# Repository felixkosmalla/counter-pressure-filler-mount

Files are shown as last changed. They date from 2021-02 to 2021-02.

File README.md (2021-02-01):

# Counter Pressure Filler Mount
Source Files and Documentation for a Mount for the Cheap Counter Pressure Fillers

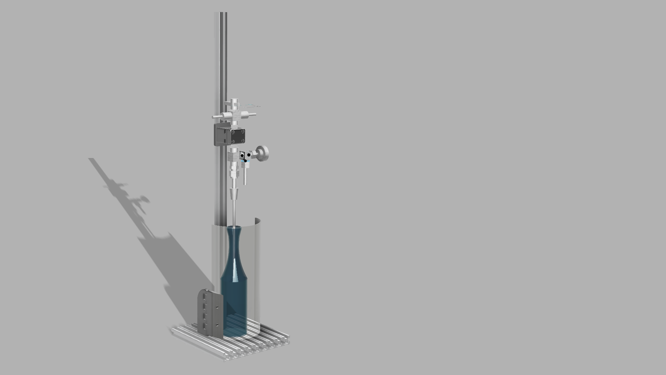
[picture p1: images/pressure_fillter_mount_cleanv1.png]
Counter Pressure Filler Mount


# Disclaimer
I assume a certain degree of self awareness, responsibility and common sense of the reader. Use these files and resources at your own risk. I am not responsible for any damage to humans and or things that may arise when using a counter pressure filler with this rig. I also do not guarantee any degree of completeness for the provided documents and files.

# Tools and Resources needed
* 3D Printer (or someone you know that has a 3D Printer), I used PETG and a Prusa MK3s, 20% infill, with supports
* Laser Cutter (optional)
* Small screwdriver to clean up 3D print
* Allen Keys
* Hot Glue Gun (or wood glue?)
* Heat Gun to form the shield
* Hammer
* 5.5mm drill bit & drill

# Bill of Material
Links for convenience, no affiliation. OpenBuilds 2020 V-Slot Profiles are used as structural base.

| Product | Link | Amount |
| --- | --- | --- |
| Counter Pressure Filler | https://www.amazon.de/gp/product/B07TQT33DP | 1 |
| Openbuilds Gantry Plate | https://www.amazon.de/dp/B07SLZFWKF | 1 |
| Angle for 2020 Openbuilds Profiles + Nuts + Bolts | gone.., maybe print it https://www.thingiverse.com/thing:105900 | 1 |
| Nuts for 2020 Openbuilds Profile | gone.., also maybe print it https://www.thingiverse.com/thing:3050607 | 2 |
| M5x10 | Hardware Store | 4 |
| M5 Nut | Hardware Store | 6 |
| M5 Nut | Hardware Store | 6 |
| 2020 OpenBuilds Profile, 20cm | https://shop.myhobby-cnc.de/bauteile/mechanische-bauteile/profile/66/openbuilds-profil-20x20mm | 9 |
| 2020 OpenBuilds Profile, 70cm | https://shop.myhobby-cnc.de/bauteile/mechanische-bauteile/profile/66/openbuilds-profil-20x20mm | 1 |
| 2mm Plexiglas, 25cm x 18.5cm | Hardware Store? | 1 |
| 3mm A3 MDF sheet or plywood | Hardware Store? | 1, maybe 2 to be sure |

# Parts to Print

## 1x Shield Mount
This part can be printed as a whole, standing up. A little carfull bending will losen the hinge. Clean it with something pointy like a flat head screwdriver.

## 1x Bottom and Top Clamp
The notches in the top clamp part need to be printed with support structures and then cleaned with a screwdriver or something [hook-y](https://www.amazon.de/dp/B07JP662XM). This is tedious, but it did fit for me in the end.
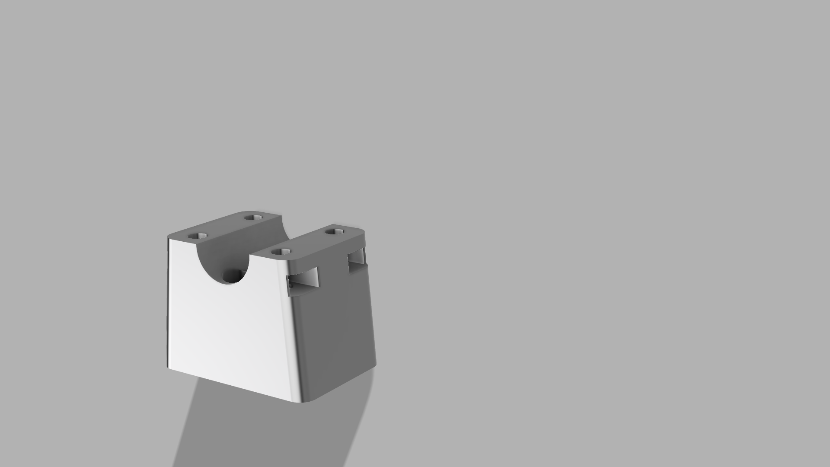
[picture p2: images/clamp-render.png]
Clamp Bottom that needs to be cleaned


## 16x OpenBuilds Connector
https://www.thingiverse.com/thing:2160166
Maybe you need to scale this, see instructions!

# Assemble

## Base
Use the OpenBuild Connectors and a little persuasian with a hammer to connect the profiles to form a base.

## Stem
Mount the stem with the angle at the 5th shorter profile.

## Shield Mount
Mount the shield mount with two nuts and bolts at the 7th profile.

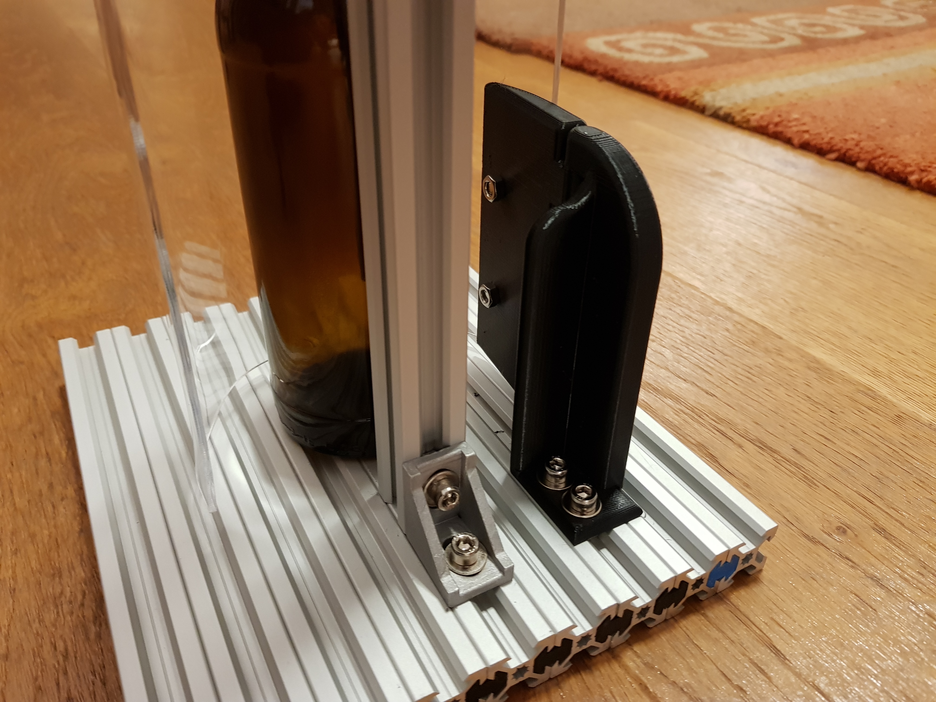
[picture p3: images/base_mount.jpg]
Assmebled base and mounted stem and shield mount


## Shield
Drill the holes according to the drawing or use a laser cuttter and the provided DXF file.
Cut 4 Rings and 6 Ribs out of the MDF according to the pattern in the PDF directory. 
Glue the bending rig together with hotglue or whatever you have at hand.
Without removing the protective layer from the plexiglass sheet, wedge the sheet in the bending rig.
**Make sure that the long end is pointing upwards.**
Start heating up the sheet and smooth, horizontal movements until the sheet starts bending. Work your way up until the sheet is completely bend around the rig.

After cooling, mount the Shield on the shield mount using the M5X10 screws.

## Clamp
Squeece 4 Nuts in the recesses of the clamp base. Mount the base on the gantry plate.
Clamp the pressure filler between the clamp base and top using 4 screws, tightening them carefulle and diagonally.
Slide the gantry on the stem.

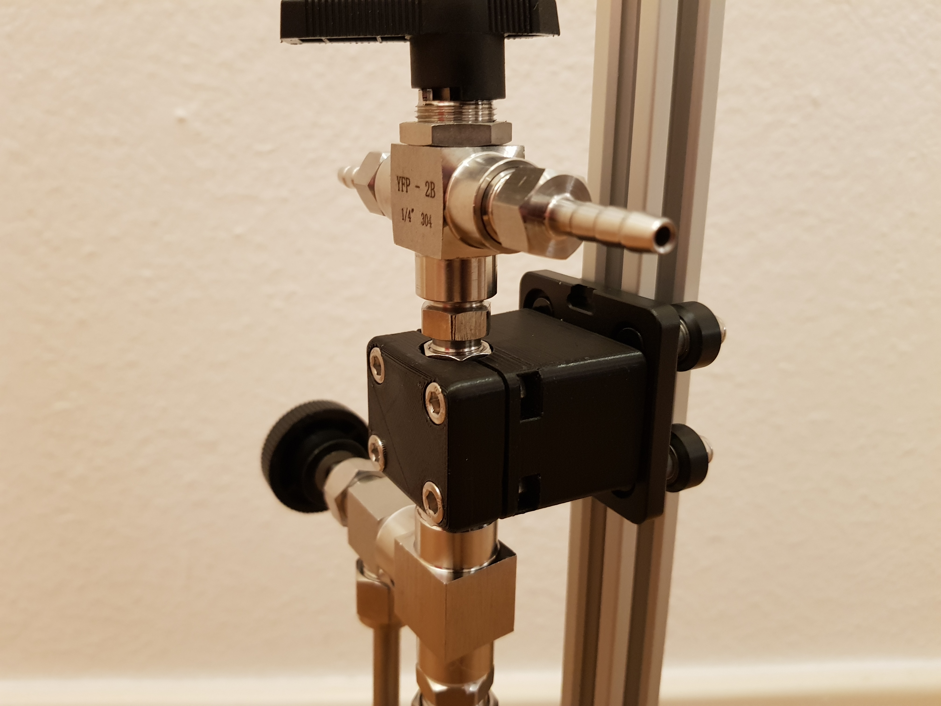
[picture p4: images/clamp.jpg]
Clamped pressure filler


# Happy Botteling!
Any comments or improvements? Either submit an issue or create a pull request. If you found this useful, consider [buying me a beer](https://paypal.me/felixkosmalla) ;) 

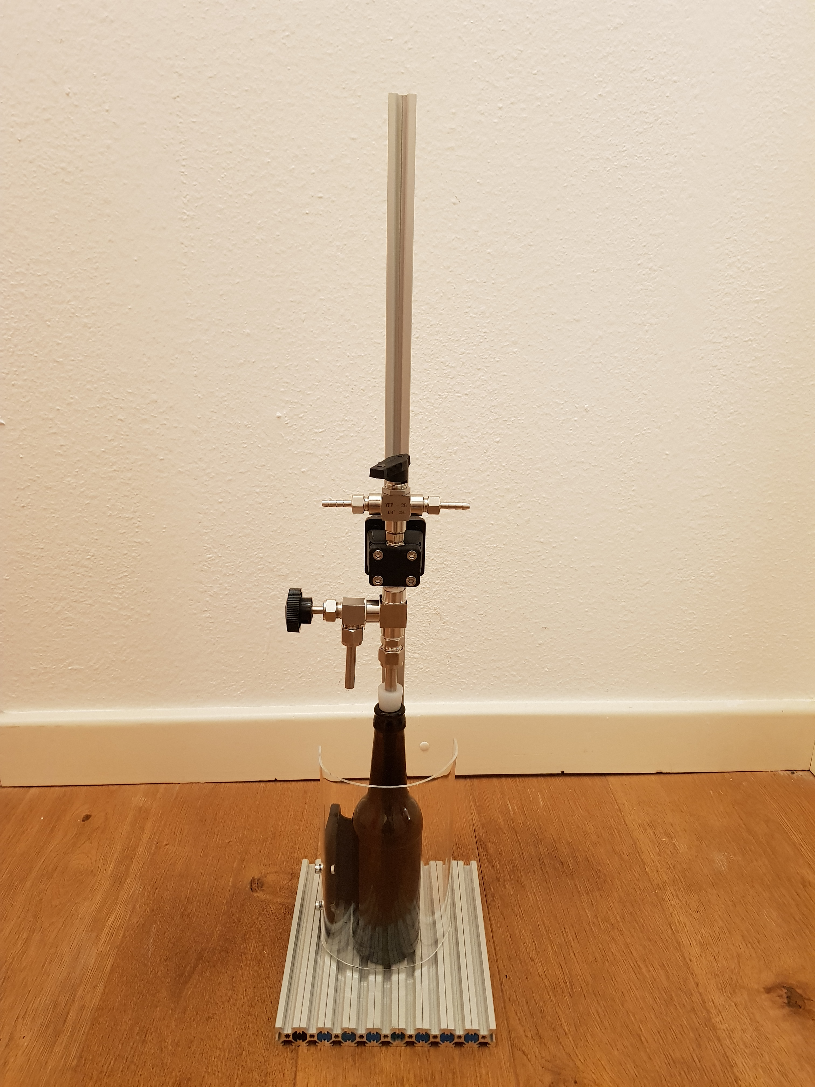
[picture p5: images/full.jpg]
pressure filler mount pressure filler mount

As you can see, I did **not** align the long side upward on the bending rig, resultin in a shorter shield towards the top that I had to cut towards the back. Don't be like me, be smart!

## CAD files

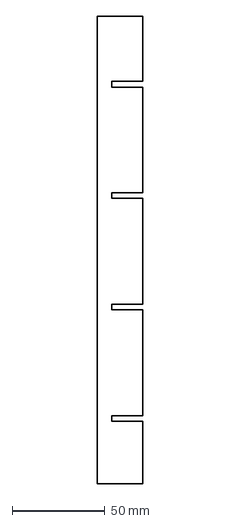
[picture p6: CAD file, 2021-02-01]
DXF/bending_frame_rib.dxf
24.8 x 251.5 mm

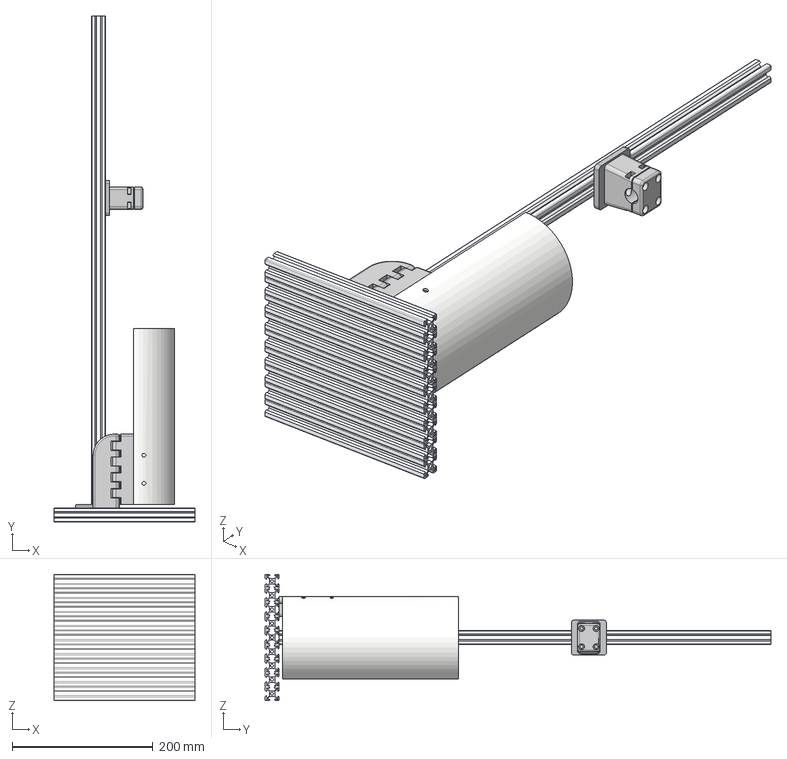
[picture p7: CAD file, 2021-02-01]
STEP Files/pressure_fillter_mount_clean v1.step
200.0 x 720.0 x 180.0 mm

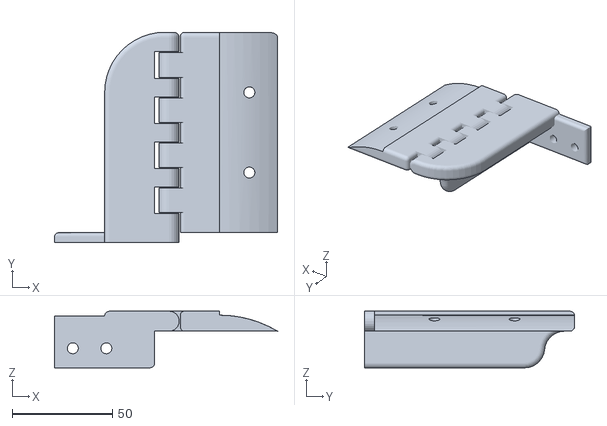
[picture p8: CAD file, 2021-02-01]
STL/shield_mount v1.stl
111.2 x 105.0 x 28.3

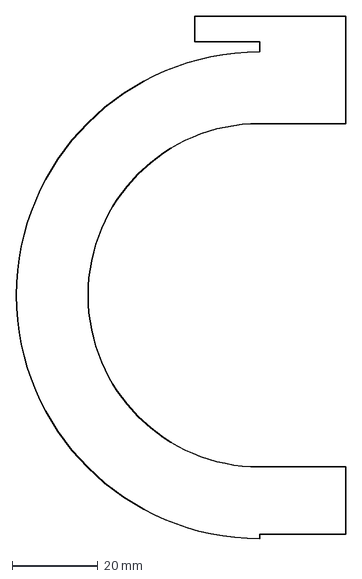
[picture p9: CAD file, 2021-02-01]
DXF/bending_frame_ring.dxf
76.7 x 121.8 mm

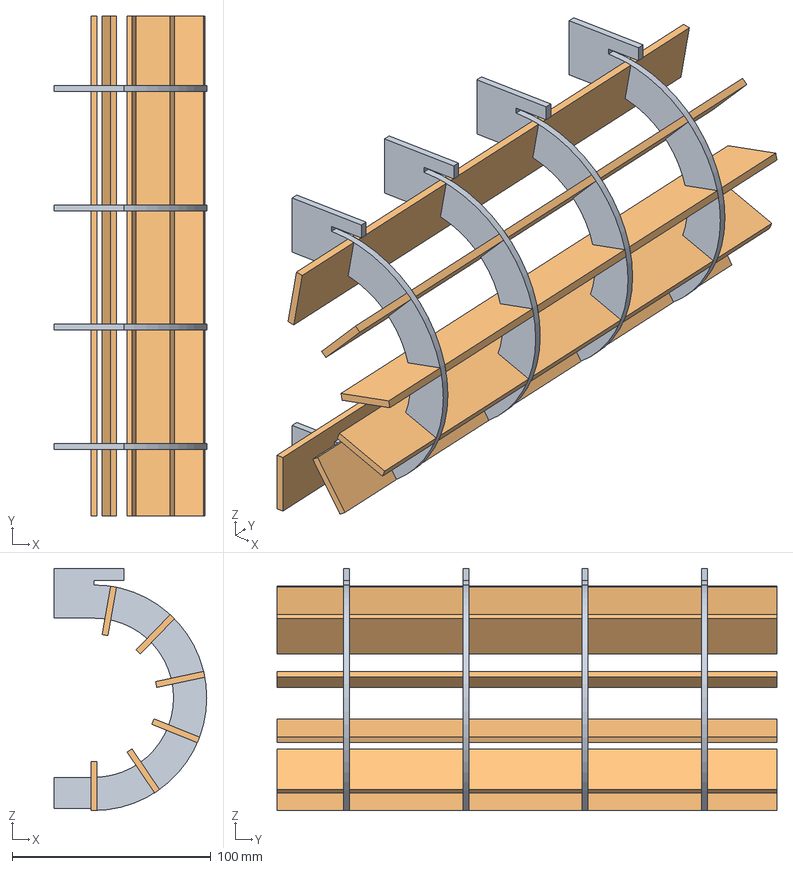
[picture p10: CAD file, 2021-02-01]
STEP Files/bending rig v7.step
76.7 x 251.5 x 121.8 mm

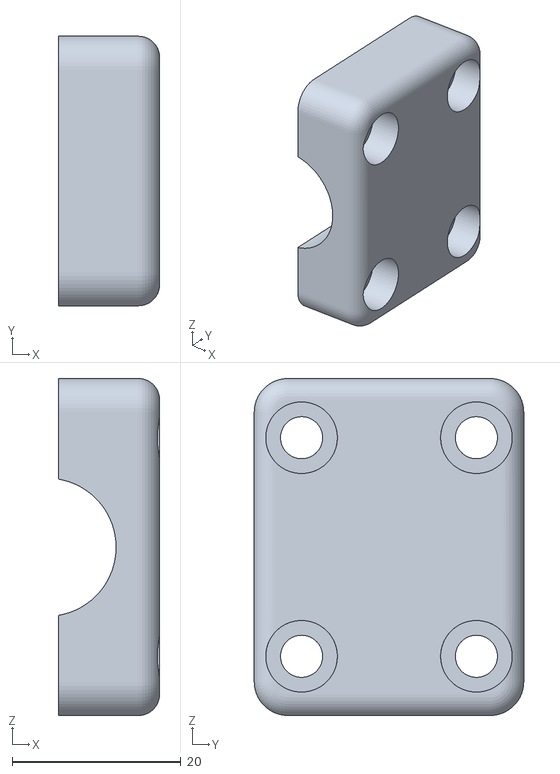
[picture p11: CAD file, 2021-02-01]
STL/bottom_clamp.stl
12.0 x 32.0 x 40.0

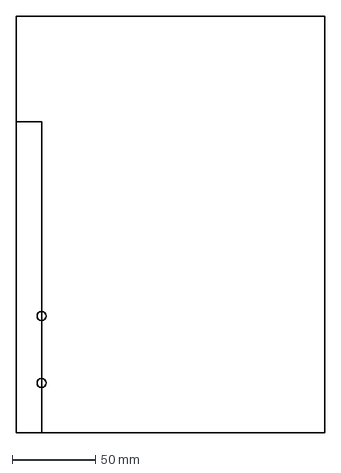
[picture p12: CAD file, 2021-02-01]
DXF/shield.dxf
185.0 x 250.0 mm

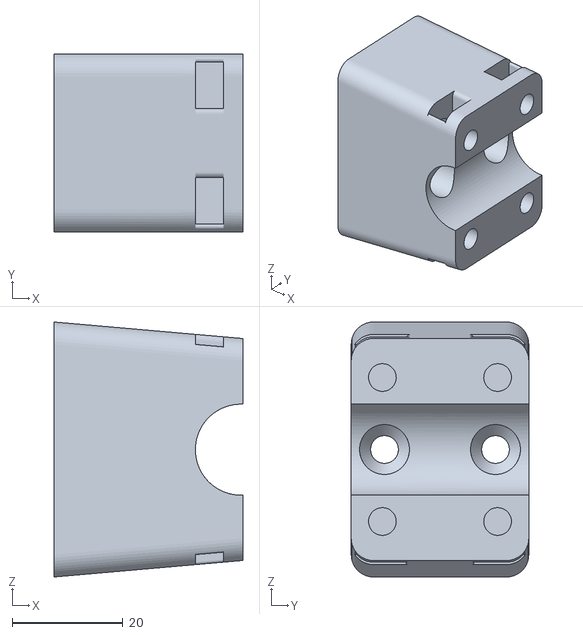
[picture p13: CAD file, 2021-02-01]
STL/top_clamp.stl
34.0 x 32.0 x 45.9

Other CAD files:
STEP Files/bending rig v1.f3d

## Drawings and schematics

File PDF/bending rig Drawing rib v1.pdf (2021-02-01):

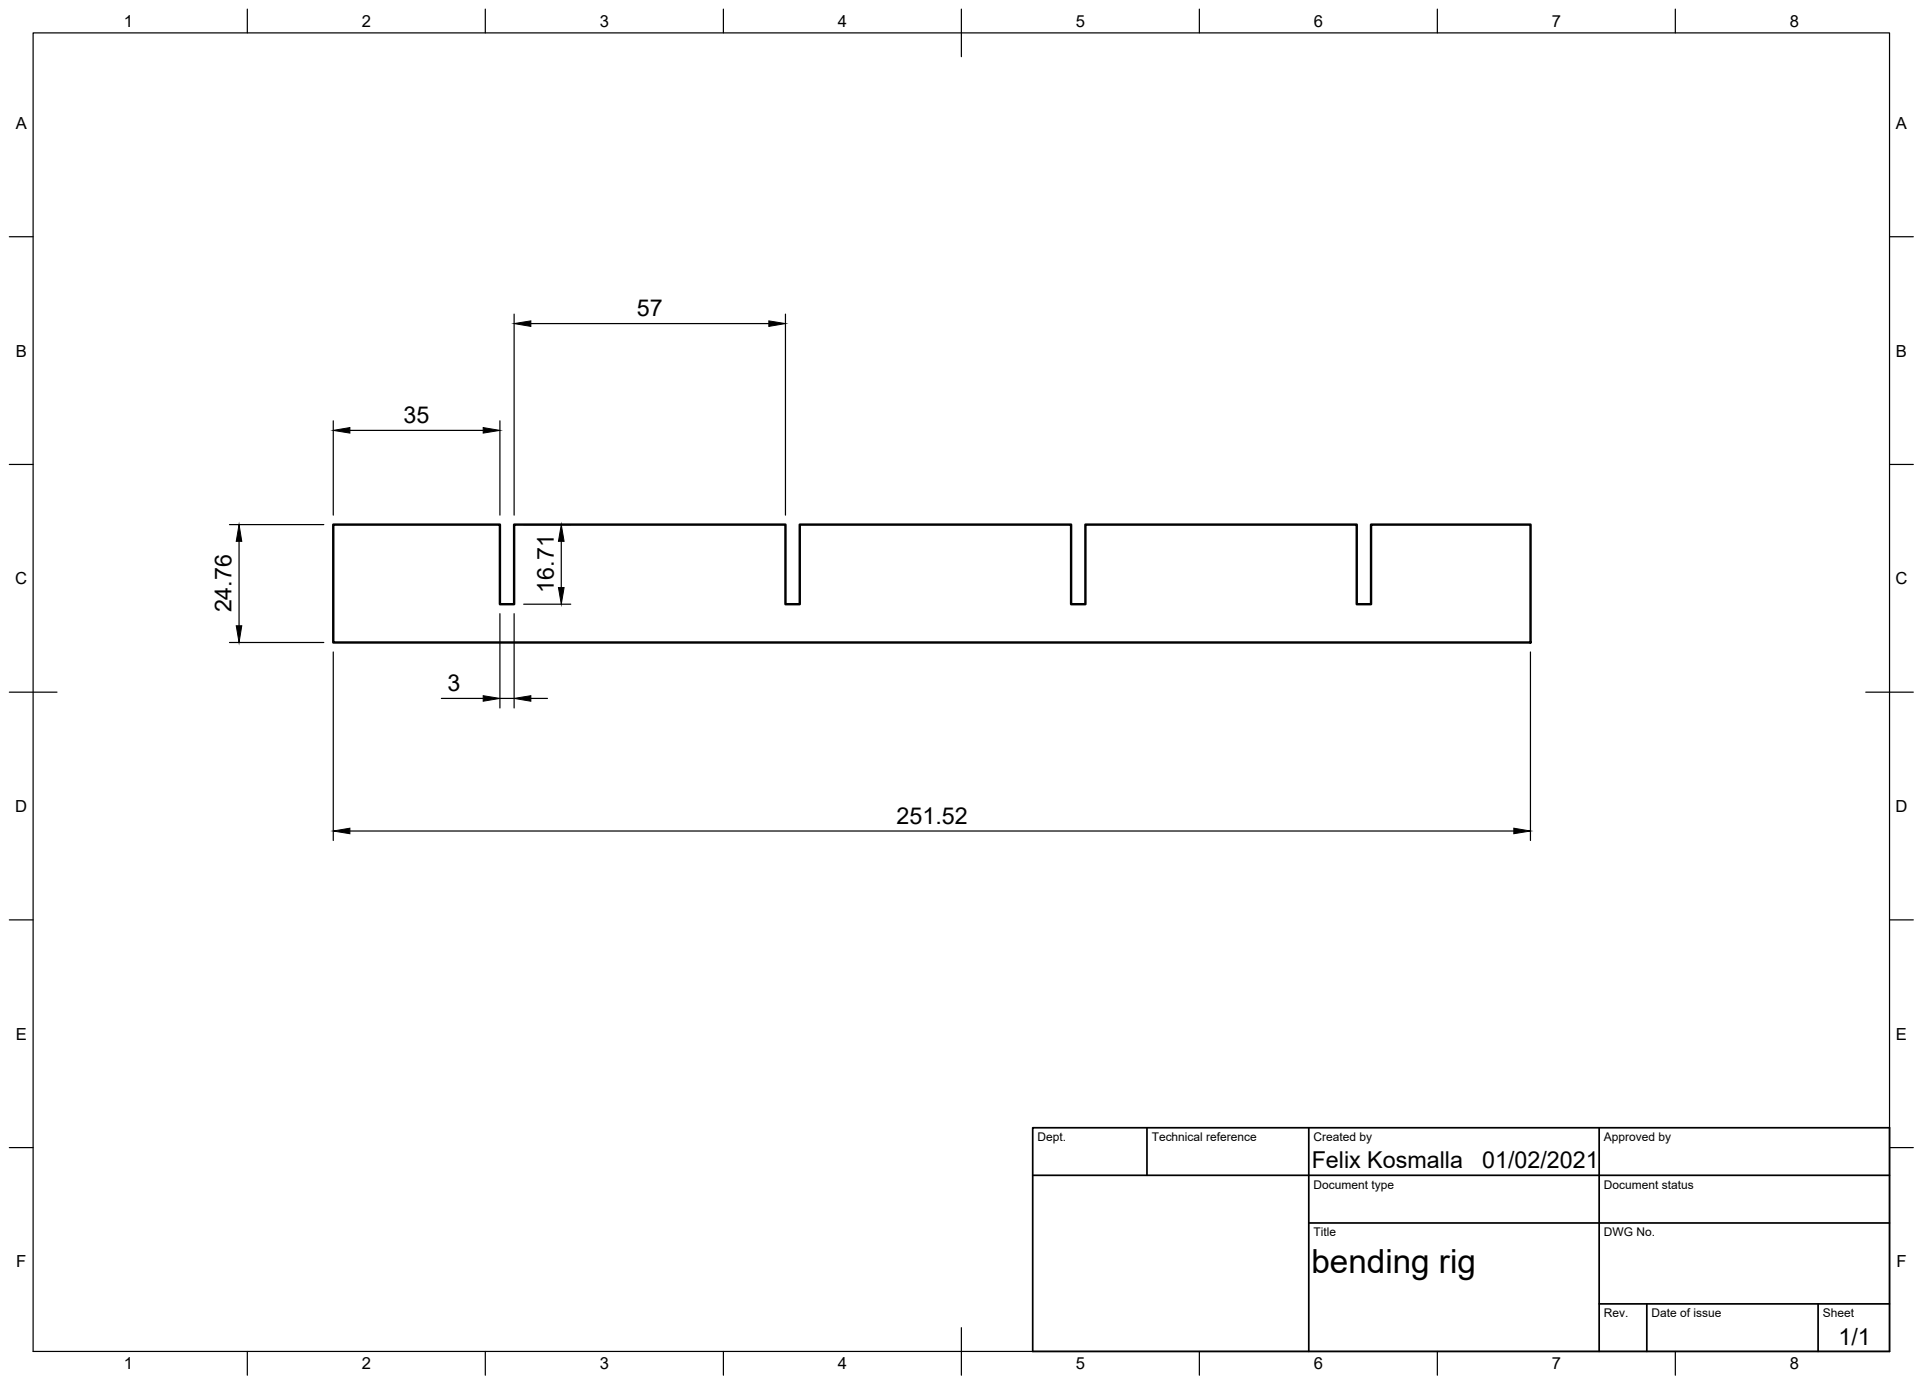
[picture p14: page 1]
Title; DWG No.; Rev.; Date of issue; Sheet; bending rig; Felix Kosmalla 24.76

Dept. | Technical reference | Created by 01/02/2021 | Approved by

Document type | Document status

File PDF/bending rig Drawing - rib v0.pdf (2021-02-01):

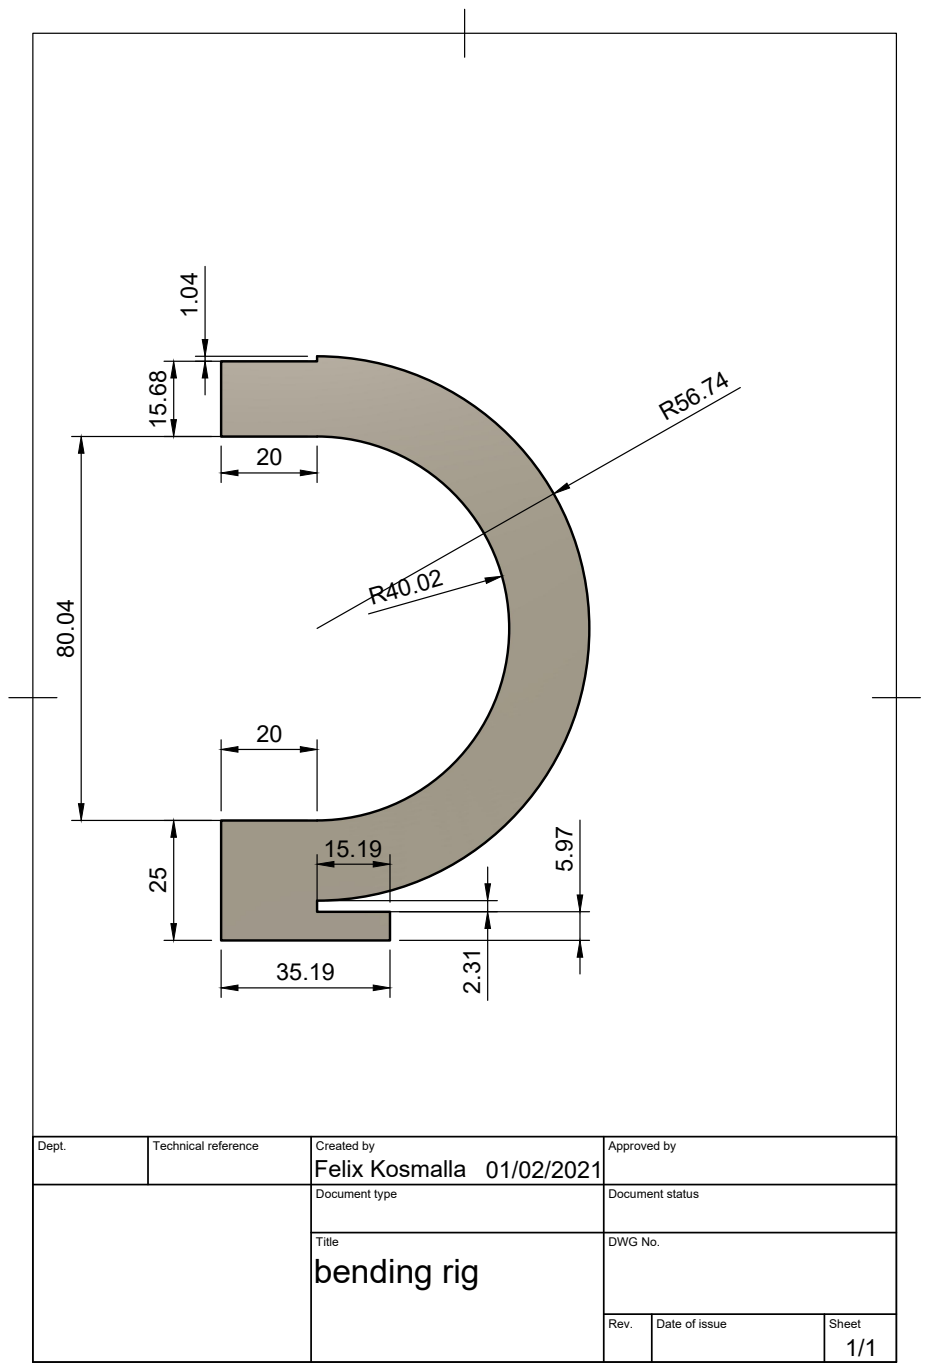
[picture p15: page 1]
Felix Kosmalla 15.68 1.04

Dept. | Technical reference | Created by 01/02/2021 | Approved by

Document type | Document status

Title bending rig | DWG No.

Rev. | Date of issue | Sheet 1/1

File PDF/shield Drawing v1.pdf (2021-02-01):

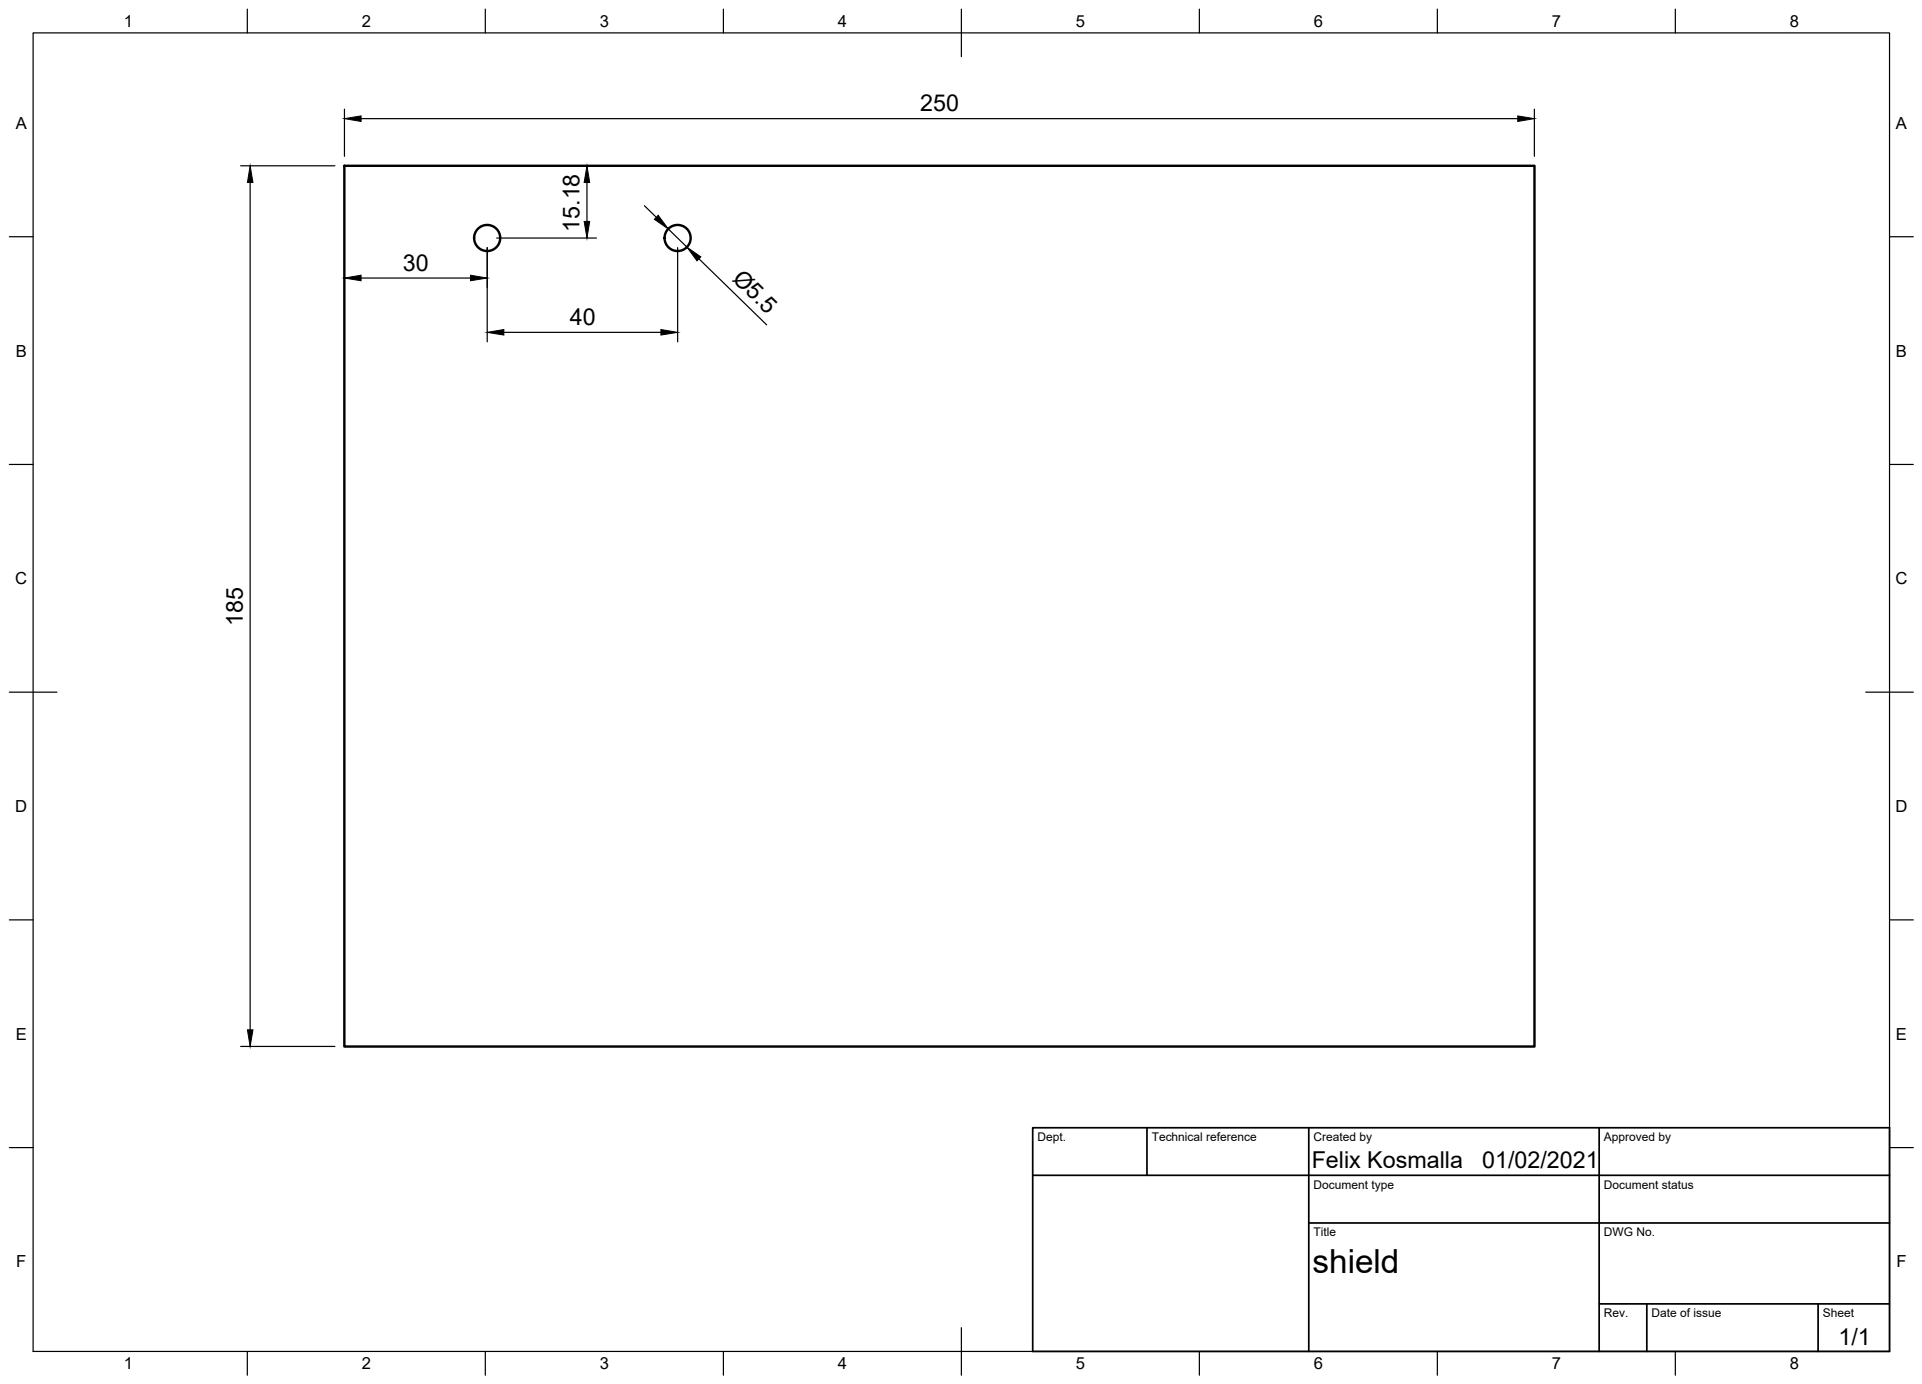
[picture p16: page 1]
Title; DWG No.; Rev.; Date of issue; Sheet

Dept. | Technical reference | Created by Felix Kosmalla 01/02/2021 | Approved by

Document type | Document status

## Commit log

2021-02-01 initial files
    [bending rig v1.f3d, bending_frame_rib.dxf, bending_frame_ring.dxf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]
2021-02-01 initial write down
    [bottom_clamp.stl, top_clamp.stl]
2021-02-01 fixed dimensions of bending rig
    [bending rig v7.step, bending_frame_rib.dxf, pressure_fillter_mount_clean v1.step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]
2021-02-01 added image of rendered clamp
